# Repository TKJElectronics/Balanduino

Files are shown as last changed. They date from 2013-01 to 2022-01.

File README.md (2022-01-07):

# Balanduino
#### Developed by TKJ Electronics 2013-2022

The code is released under the GNU General Public License.
_________

This is the code for the Balanduino, the Open Source Balancing robot.

# Arduino compatible

To use the Balanduino as a normal Arduino board you need to add the hardware add-on to the Arduino IDE.

See the [Getting Started page](http://balanduino.tkjelectronics.dk/get-started) for more information.

# Hardware

The Balanduino hardware consist of an ATmega1284P running at 10MHz.

A MPU-6050 3-axis accelerometer and gyroscope.
The accelerometer and gyroscope readings are combined using a Kalman filter library. See my blog post: <http://blog.tkjelectronics.dk/2012/09/a-practical-approach-to-kalman-filter-and-how-to-implement-it/> and source <https://github.com/TKJElectronics/KalmanFilter> for more information.

USB Host support is implemented using the MAX3421E and the USB Host library: <https://github.com/felis/USB_Host_Shield_2.0>.

Two VNH5180 motor controller ICs is used to drive the two motors.

More information can be found at the Wiki article: <http://balanduino.tkjelectronics.dk/wiki/Overview>.

# Remote control

## Game controllers

To control the robot you can use the following game controllers:

* Normal PS3 Dualshock controller
* PS3 Navigation controller
* PS3 Move controller
* PS4 controller
* Xbox 360 wireless controller
* Wiimote including support for the Motion Plus and Nunchuck extension
* Wii U Pro controller

### Pairing

To pair with any of the PS3 controller please see the following section of the USB Host library readme: <https://github.com/felis/USB_Host_Shield_2.0#ps3-library>.

To pair with the PS4 controller send: ```CPP;``` via the serial monitor. Then hold down the Share button and then hold down the PS button without releasing the Share button. The PS4 controller will then start to blink rapidly indicating that it is in paring mode.

To use a Xbox 360 wireless controller you need a special receiver. More information can be seen at the following link: <https://github.com/felis/USB_Host_Shield_2.0#xbox-360-library>.

To pair with the Wiimote send: ```CPW;``` via the serial monitor and then press 1 and 2 at the same time on the Wiimote. On the Wii U Pro controller you should press on the sync button instead.

## Android App

It it also possible to control the robot and adjust the PID values and others variables using the following Android application:



Source: <https://github.com/TKJElectronics/BalanduinoAndroidApp>

## Computer applications

You can also use your Windows, Mac or Linux based computer by using the following Processing application: <https://github.com/TKJElectronics/BalanduinoProcessingApp>.

A dedicated Windows application is also available: <https://github.com/TKJElectronics/BalanduinoWindowsApp>.

## RC Transmitter

You can also use a RC transmitter. For now only Spektrum satellite receivers are supported.

You will need the following receiver and cable:

* <http://hobbyking.com/hobbyking/store/__46339__OrangeRx_R100_Spektrum_JR_DSM2_Compatible_Satellite_Receiver.html>
* <http://hobbyking.com/hobbyking/store/__24524__ZYX_S_DSM2_DSMJ_Satellite_Receiver_Cable.html>

After that simply connect the red wire to 5V, black to GND and the yellow one to RX0.

To bind with the satellite receiver send ```BS;``` via the serial monitor and then follow the instructions.

Note that you might need to disconnect the satellite receiver from RX0 if it is already sending data, as it will corrupt your command.

The video below shows a video demonstration of it being used together with some FPV equipment:

<a href="http://www.youtube.com/watch?v=tcFdWlAbc3s" target="_blank">Balanduino FPV demonstration</a>

# Video presentation

A video for the Kickstarter presentation can be seen below:

<a href="http://www.youtube.com/watch?v=_kQniPbg9zc" target="_blank">Kickstarter video presentation</a>

A video filmed with a GoPro mounted on the robot can be seen below:

<a href="http://www.youtube.com/watch?v=CvFcnb_9anM" target="_blank">GoPro demonstration</a>

# Calibration of the accelerometer

If the robot tilts to one of the sides when you receive the kit, you might need to calibrate the accelerometer.

This is done by simply sending ```AC;``` via the serial monitor. After that simply just follow the instructions.

# Download

To download the entire repository including all submodules run the following command in a terminal:

```bash
curl https://raw.githubusercontent.com/TKJElectronics/Balanduino/master/download.sh | sh
```

Or simply download the latest release: <https://github.com/TKJElectronics/Balanduino/releases/download/1.2.0/Balanduino-1.2.0.zip>.

If you want to clone the project then use the recursive command to clone all the submodules as well:

```bash
git clone --recursive https://github.com/TKJElectronics/Balanduino.git
```

</br>

For more information visit the official website: <http://balanduino.tkjelectronics.dk/>, the forum: <http://balanduino.tkjelectronics.dk/forum> or feel free to contact us at <support@tkjelectronics.dk>.

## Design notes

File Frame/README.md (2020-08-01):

# Balanduino Frame
#### Developed by Kristian Lauszus and Thomas Jespersen, TKJ Electronics 2013-2015

The frame is released under the [Attribution-NonCommercial-ShareAlike 3.0 Unported](http://creativecommons.org/licenses/by-nc-sa/3.0/).
_________

This is the drawings for the three laser cut layers used for the Balanduino.

To open the files you will need to download and install [SolidWorks](http://www.solidworks.com/) or you can also import the .DXF file into any preferred CAD program.

For more information visit the official website: <http://balanduino.net/>, the forum: <http://forum.balanduino.net/> or feel free to contact us at <support@tkjelectronics.dk>.

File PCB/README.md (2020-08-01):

# Balanduino PCB
#### Developed by Kristian Lauszus and Thomas Jespersen, TKJ Electronics 2013-2015

The PCB is released under the [Attribution-NonCommercial-ShareAlike 3.0 Unported](http://creativecommons.org/licenses/by-nc-sa/3.0/).
_________

This is the PCB for the Balanduino.

To open the files you will need to download and install [EAGLE](http://www.cadsoftusa.com/download-eagle/).

For more information visit the official website: <http://balanduino.net/>, the forum: <http://forum.balanduino.net/> or feel free to contact us at <support@tkjelectronics.dk>.

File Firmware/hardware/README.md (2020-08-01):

# Balanduino hardware add-on
#### Developed by Kristian Lauszus, TKJ Electronics 2013-2020

The code is released under the GNU General Public License.
_________

This is the Balanduino hardware add-on for the Arduino IDE.

See the [Getting Started page](http://balanduino.tkjelectronics.dk/get-started) for more information.

For more information see the following sites: <http://www.arduino.cc/en/Guide/Environment#thirdpartyhardware>, <http://code.google.com/p/arduino/wiki/Platforms1>, and <https://github.com/arduino/Arduino/wiki/Arduino-IDE-1.5---3rd-party-Hardware-specification> or send us an email at <support@tkjelectronics.dk>.

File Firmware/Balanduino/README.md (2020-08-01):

# Balanduino Arduino code
#### Developed by Kristian Lauszus, TKJ Electronics 2013-2020

The code is released under the GNU General Public License.
_________

This is the Arduino code for the Balanduino balancing robot.

To compile the sketch you will need the newest version of the [Arduino IDE](http://arduino.cc/en/Main/Software).

Then open the sketch by clicking on [Balanduino.ino](Balanduino.ino).

See the [Getting Started page](http://balanduino.tkjelectronics.dk/get-started) for more information.

Advanced users can also use the included [Makefile](Makefile) if they prefer.

[Balanduino_rev12.hex](Balanduino_rev12.hex) and [Balanduino_rev13.hex](Balanduino_rev13.hex) contains the latest compiled code for revision 1.2 and older and revision 1.3 respectively.

For more information visit the official website: <http://balanduino.tkjelectronics.dk>, the forum: <http://balanduino.tkjelectronics.dk/forum> or feel free to contact us at <support@tkjelectronics.dk>.

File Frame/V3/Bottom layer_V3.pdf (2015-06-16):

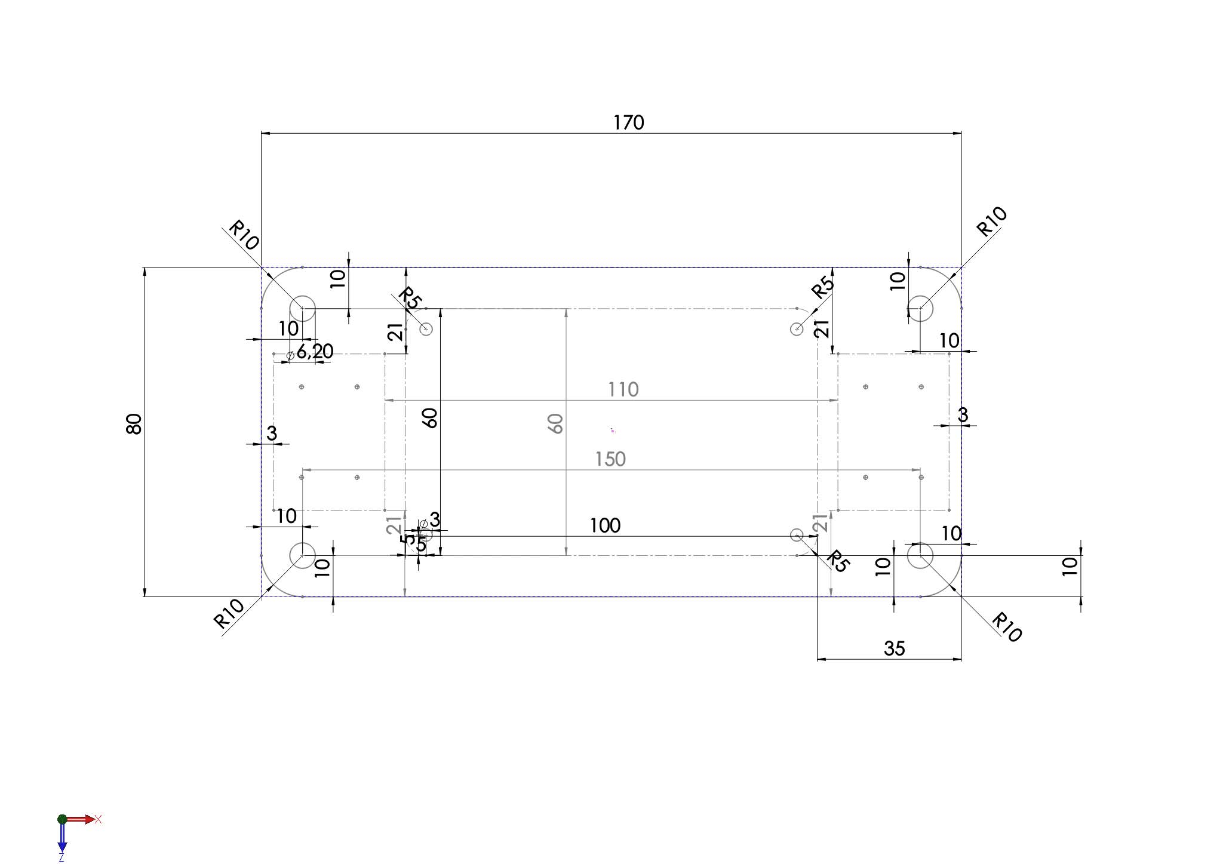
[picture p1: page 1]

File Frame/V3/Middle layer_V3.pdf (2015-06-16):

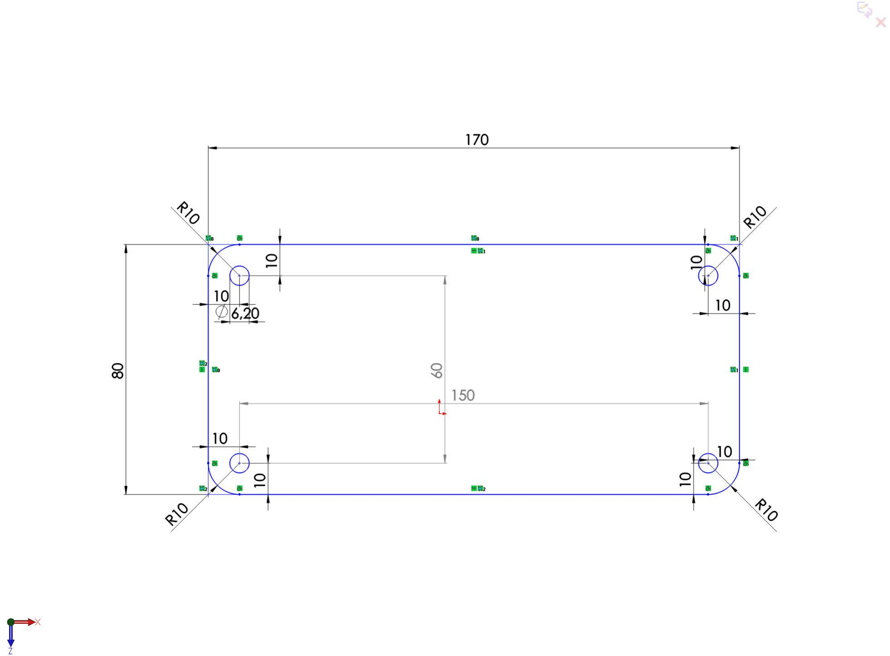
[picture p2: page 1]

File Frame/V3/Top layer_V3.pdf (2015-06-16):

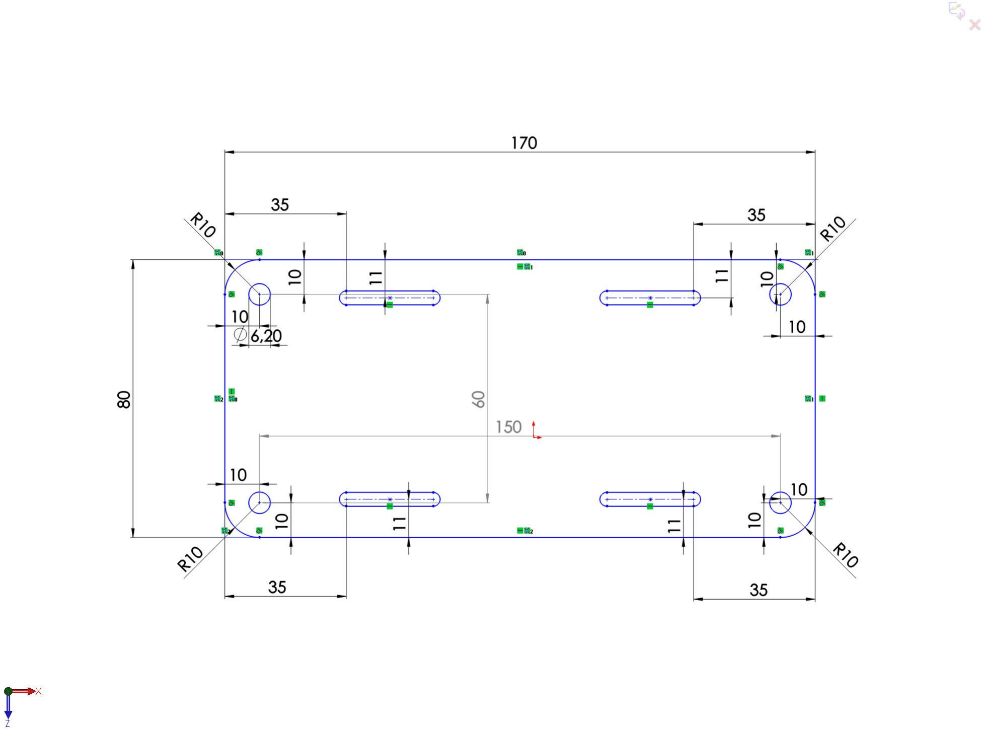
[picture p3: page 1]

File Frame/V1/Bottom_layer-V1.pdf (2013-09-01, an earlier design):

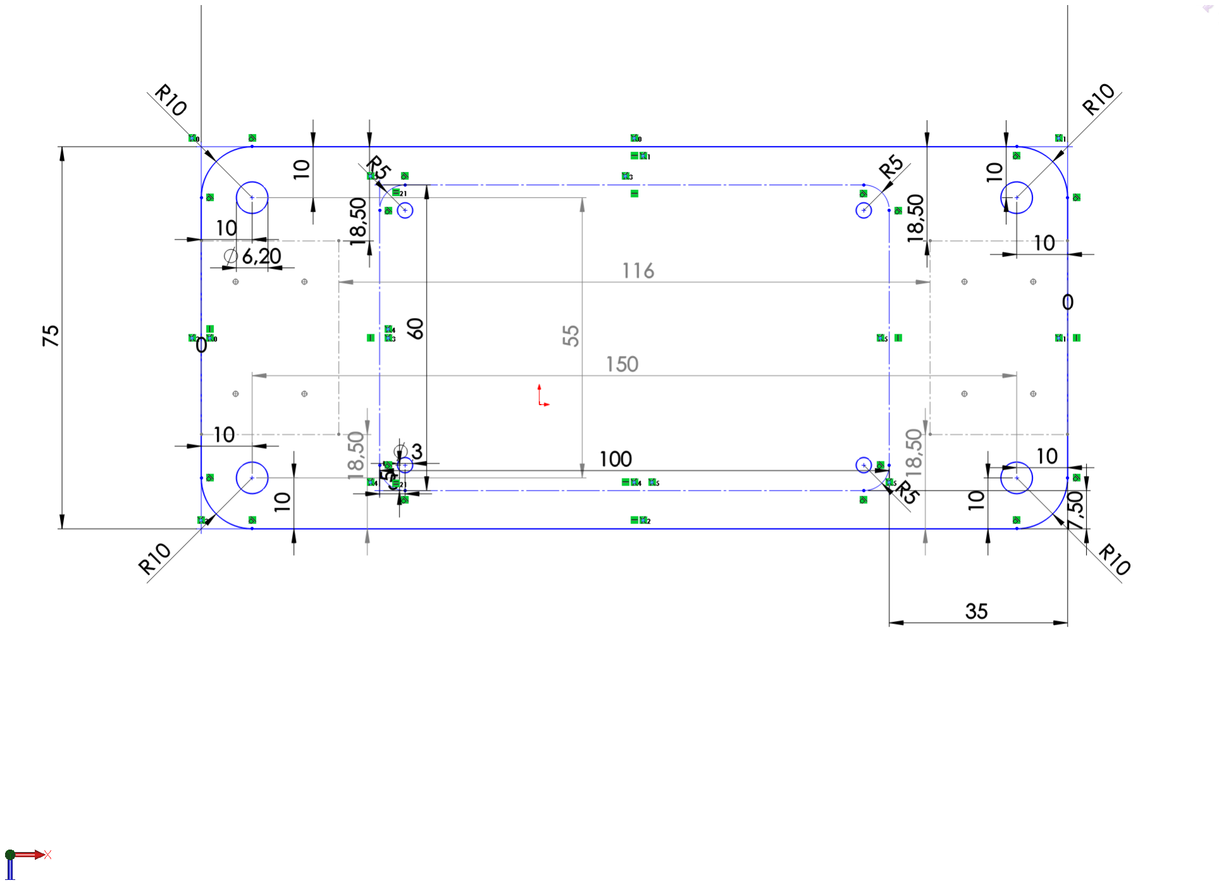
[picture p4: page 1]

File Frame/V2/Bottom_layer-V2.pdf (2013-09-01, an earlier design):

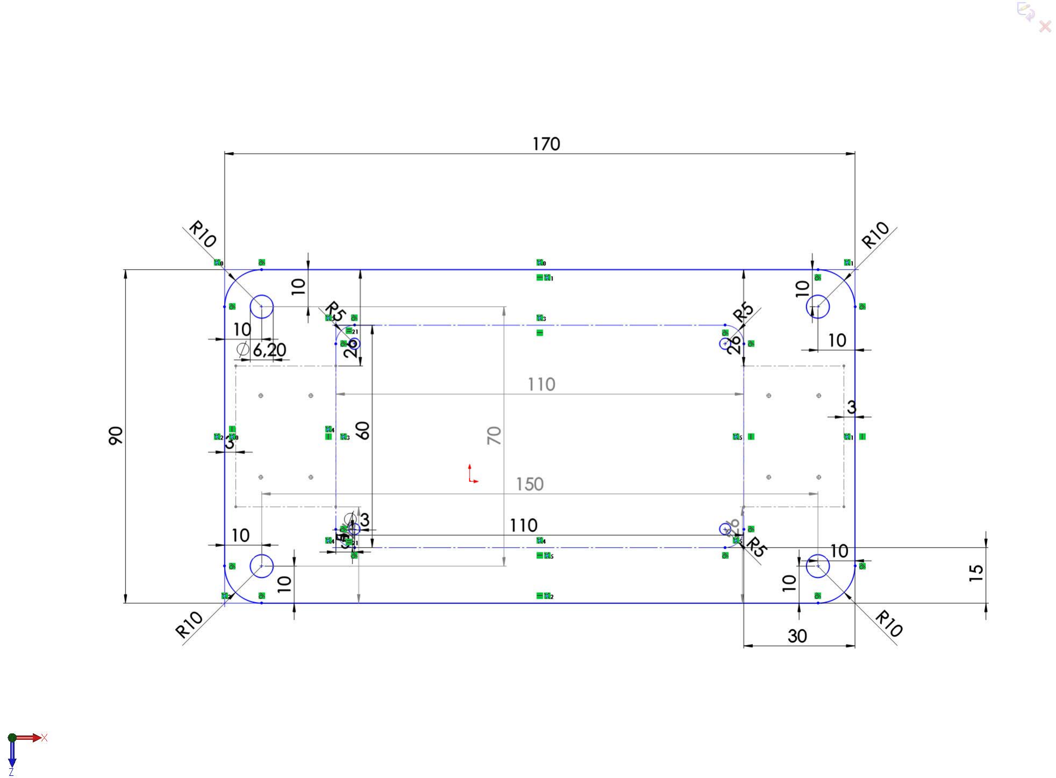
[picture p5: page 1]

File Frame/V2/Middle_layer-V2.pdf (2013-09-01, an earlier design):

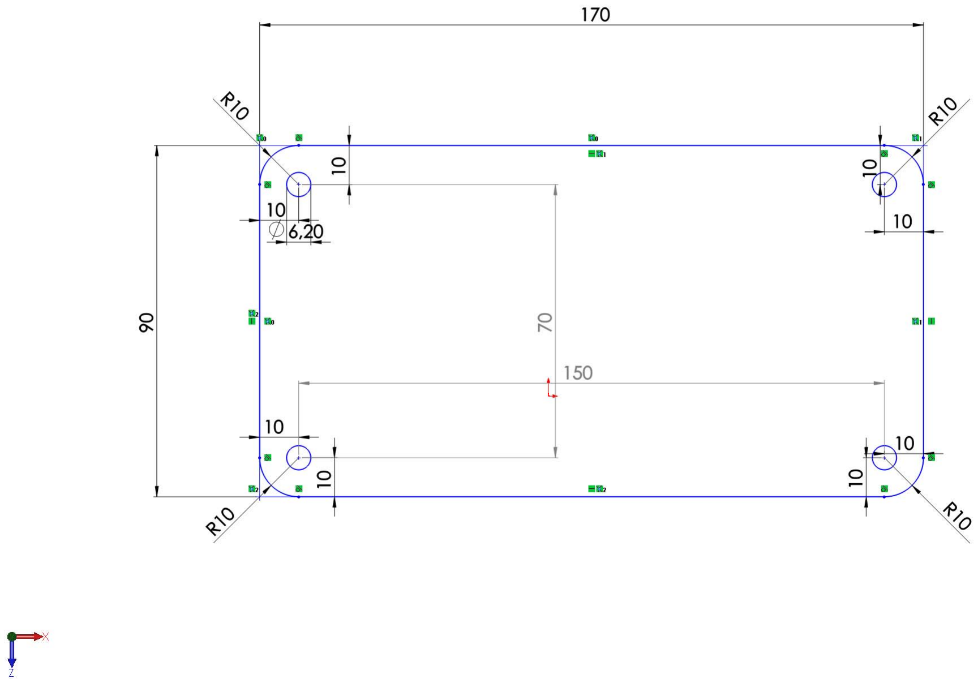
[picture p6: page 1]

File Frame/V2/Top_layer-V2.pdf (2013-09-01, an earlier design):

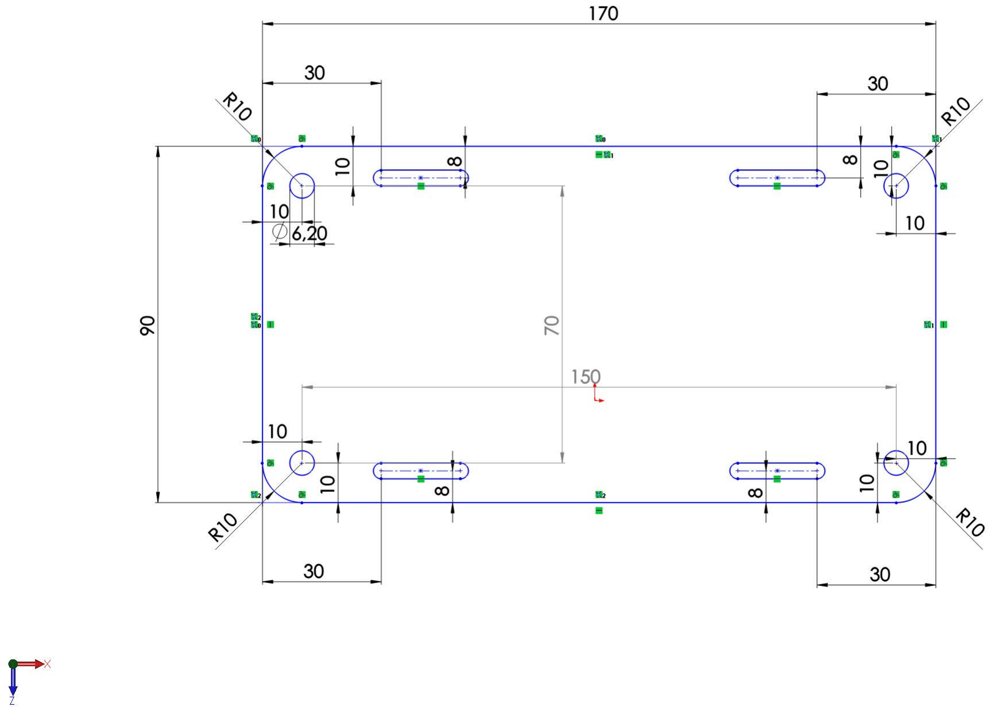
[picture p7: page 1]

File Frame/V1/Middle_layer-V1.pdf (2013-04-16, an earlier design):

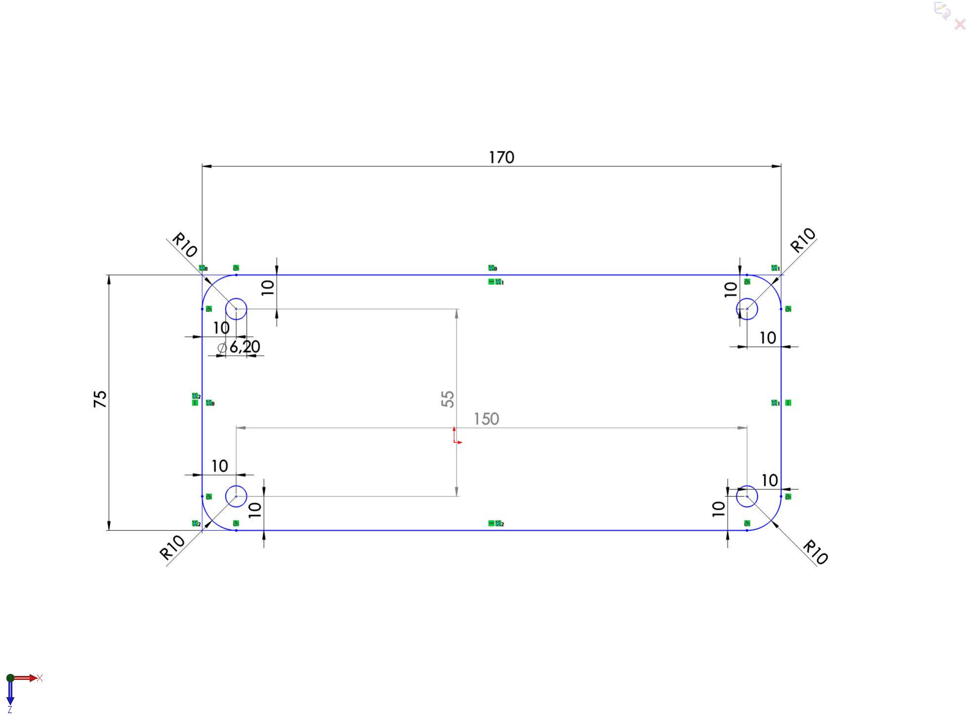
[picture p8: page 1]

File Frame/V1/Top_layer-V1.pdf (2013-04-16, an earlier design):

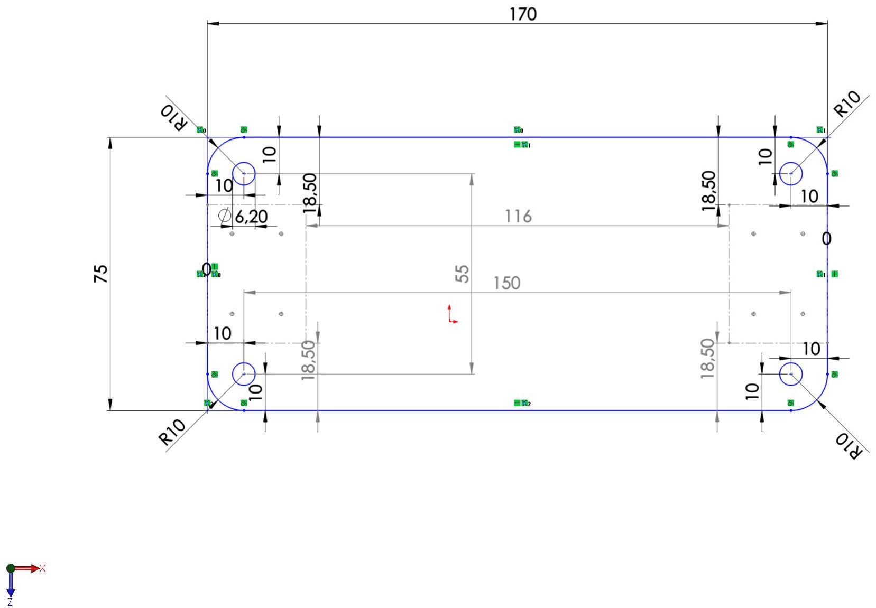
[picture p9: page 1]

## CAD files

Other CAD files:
Frame/V3/Top layer_V3.SLDPRT
Frame/V3/Bottom layer_V3.SLDPRT
Frame/V3/Middle layer_V3.SLDPRT
Frame/V1/Top_layer-V1.SLDPRT
Frame/V2/Top_layer-V2.SLDPRT
Frame/V1/Bottom_layer-V1.SLDPRT
Frame/V2/Middle_layer-V2.SLDPRT
Frame/V1/Middle_layer-V1.SLDPRT
Frame/V2/Bottom_layer-V2.SLDPRT
Frame/V1/Bottom_layer-V1.DXF
Frame/V1/Middle_layer-V1.DXF
Frame/V1/Top_layer-V1.DXF
Frame/V2/Bottom_layer-V2.DXF
Frame/V2/Middle_layer-V2.DXF
Frame/V2/Top_layer-V2.DXF
Frame/V3/Bottom layer_V3.DXF
Frame/V3/Middle layer_V3.DXF
Frame/V3/Top layer_V3.DXF

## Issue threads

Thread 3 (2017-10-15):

No waiting needed after Wire.requestFrom().

Koepel, 2017-10-15:
See: https://github.com/TKJElectronics/KalmanFilter/issues/9

Lauszus, 2018-06-23:
Since this does not have real benefits and the code in the library have been proven to work with multiple different kind of microcontrollers, then I see no real benefit by changing it. If you really want to change it, then you can submit a PR and do some testing.

Closed 2018-06-23.

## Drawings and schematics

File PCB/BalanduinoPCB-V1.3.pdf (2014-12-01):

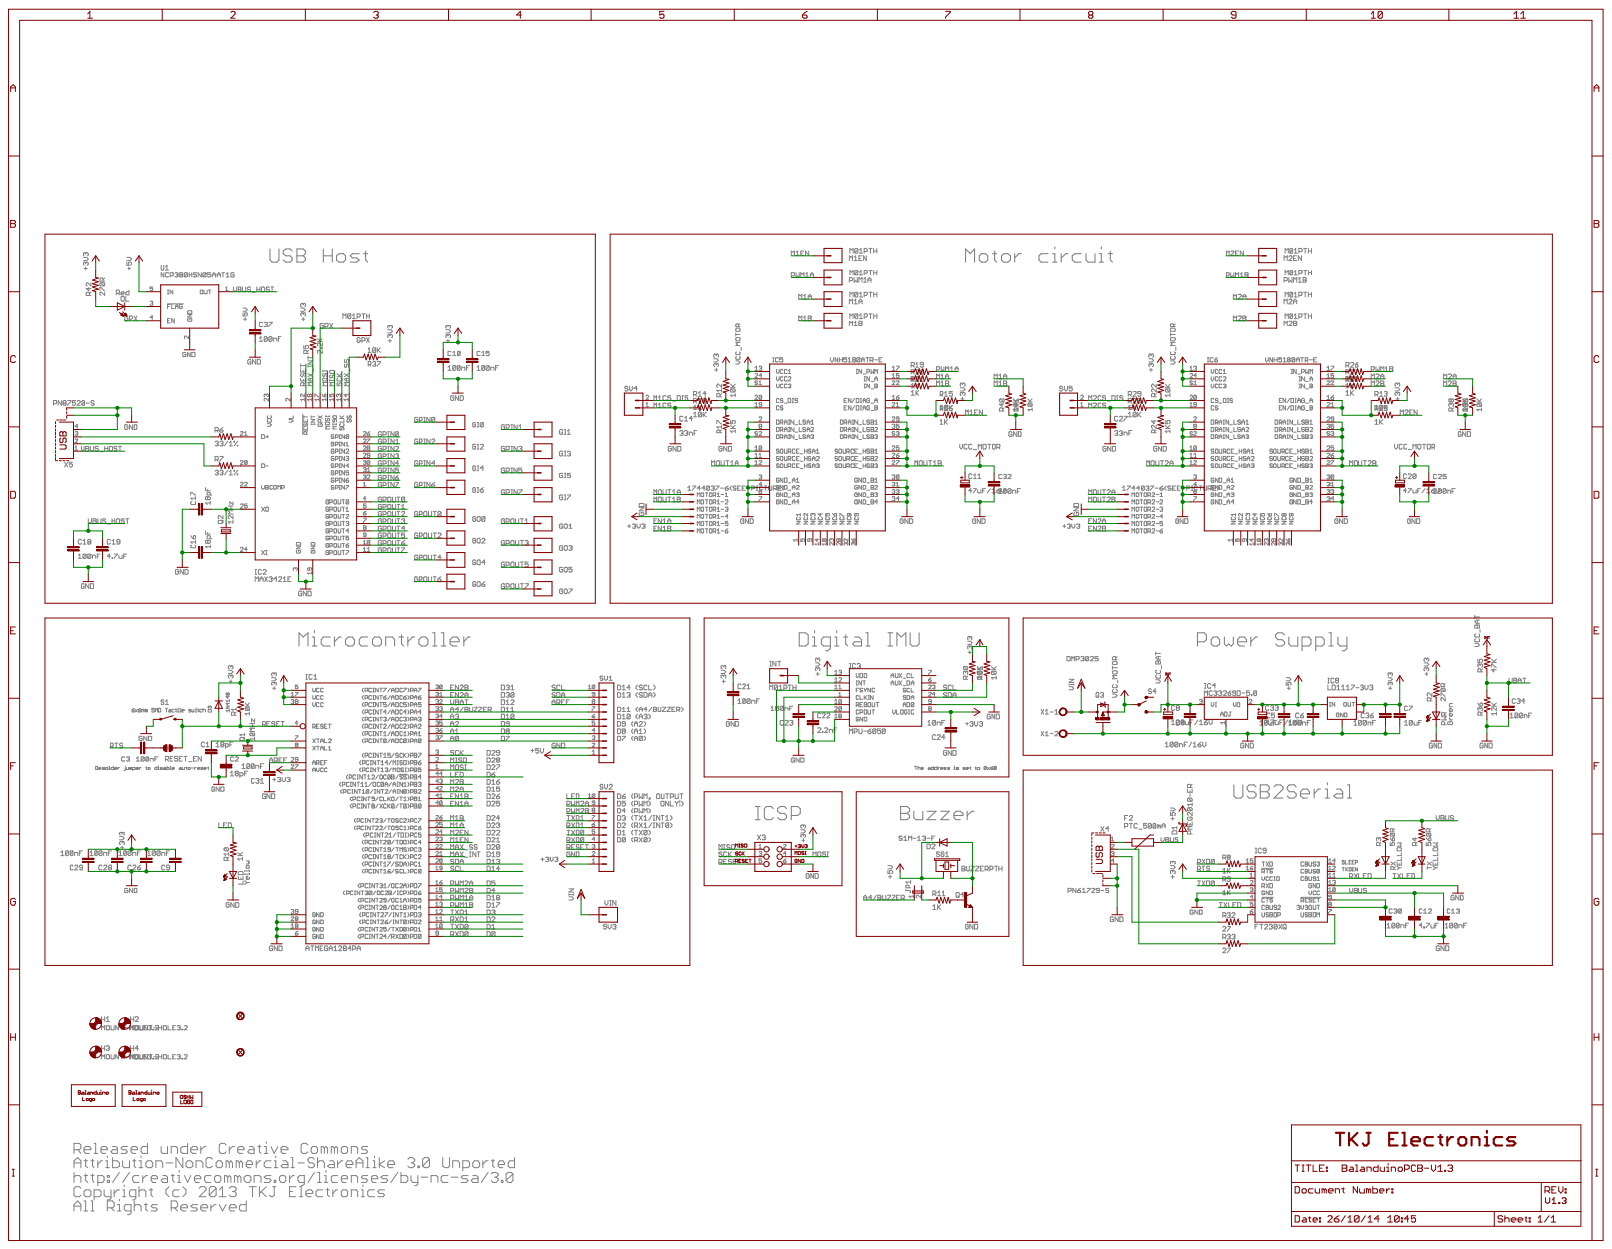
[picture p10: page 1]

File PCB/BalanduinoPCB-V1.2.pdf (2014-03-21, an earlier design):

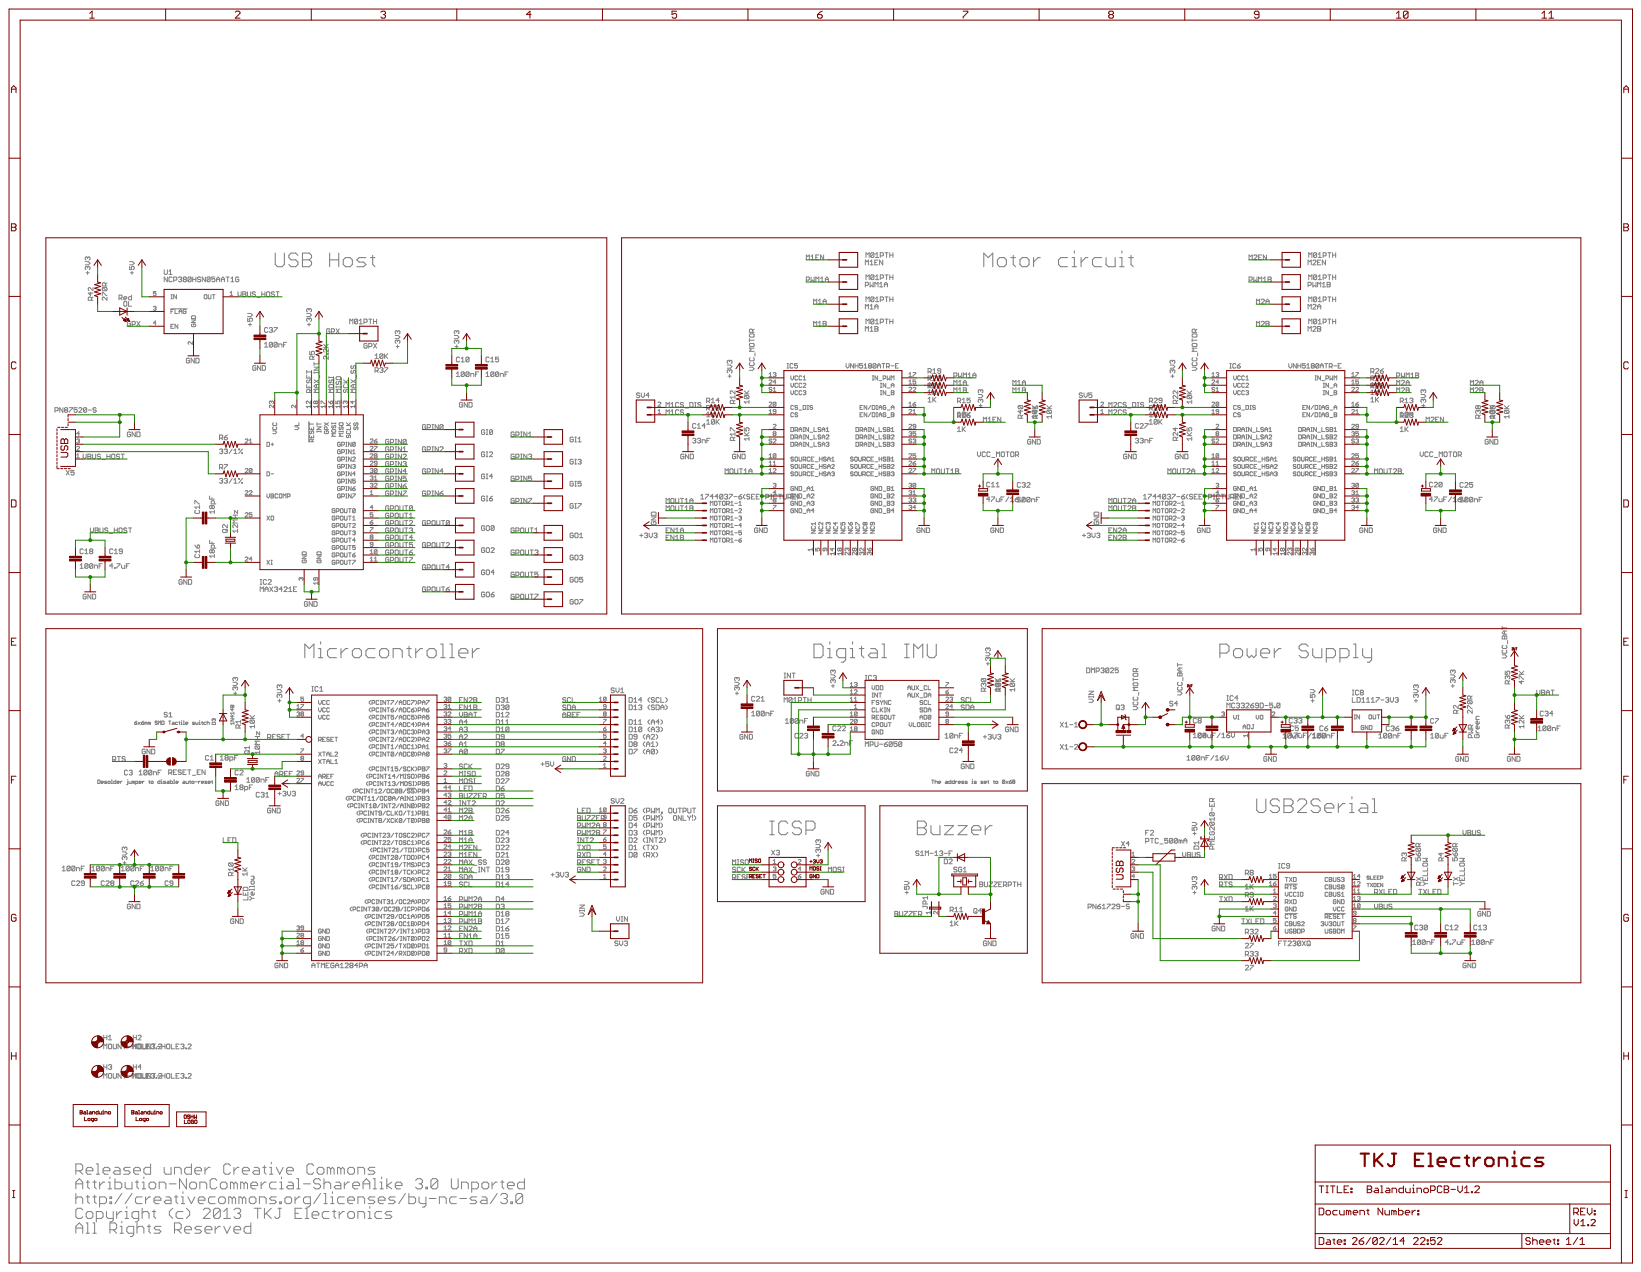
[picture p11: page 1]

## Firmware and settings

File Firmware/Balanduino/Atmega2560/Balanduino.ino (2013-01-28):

/*
 * The code is released under the GNU General Public License.
 * Developed by Kristian Lauszus
 * This is the algorithm for the Balanduino balancing robot.
 * It can be controlled by either an Android app or a Processing application via bluetooth.
 * The Android app can be found at the following link: https://github.com/TKJElectronics/BalanduinoAndroidApp
 * The Processing application can be found here: https://github.com/TKJElectronics/BalanduinoProcessingApp
 * It can also be controlled by a PS3, Wii or a Xbox controller
 * For details, see http://blog.tkjelectronics.dk/2012/02/the-balancing-robot/
 */

#include "Balanduino.h"

/* 
 * These are all open source libraries written by Kristian Lauszus, TKJ Electronics
 * The USB libraries are located at the following link: https://github.com/felis/USB_Host_Shield_2.0
 */
#include <Kalman.h> // Kalman filter library see: http://blog.tkjelectronics.dk/2012/09/a-practical-approach-to-kalman-filter-and-how-to-implement-it/
#include <XBOXRECV.h>
#include <SPP.h>
#include <PS3BT.h>
#include <Wii.h>

// Create the Kalman library instance
Kalman kalman; // See https://github.com/TKJElectronics/KalmanFilter for source code

// This will take care of all USB communication
USB Usb;

// You have to connect a Xbox wireless receiver to the Arduino to control it with a wirelessly Xbox controller
XBOXRECV Xbox(&Usb); // Uncomment DEBUG in "XBOXRECV.cpp" to save space
BTD Btd(&Usb); // This is the main Bluetooth library, it will take care of all the Bluetooth communication - Uncomment DEBUG in "BTD.cpp" to save space
SPP SerialBT(&Btd,"Balanduino","0000"); // Also uncomment DEBUG in "SPP.cpp"
PS3BT PS3(&Btd,0x00,0x15,0x83,0x3D,0x0A,0x57); // Also remember to uncomment DEBUG in "PS3BT.cpp" to save space
WII Wii(&Btd); // Also uncomment DEBUG in "Wii.cpp"

// You have to pair with your Wiimote first by creating the instance like this and the press 1+2 on the Wiimote - you only have to do this once
//WII Wii(&Btd,PAIR);

void setup() {
  /* Setup encoders */
  pinMode(leftEncoder1,INPUT);
  pinMode(leftEncoder2,INPUT);
  pinMode(rightEncoder1,INPUT);
  pinMode(rightEncoder2,INPUT); 
  attachInterrupt(0,leftEncoder,RISING); // pin 2
  attachInterrupt(1,rightEncoder,RISING); // pin 3

  /* Setup motor pins to output */
  sbi(leftPwmPortDirection,leftPWM);
  sbi(leftPortDirection,leftA);
  sbi(leftPortDirection,leftB);
  sbi(rightPwmPortDirection,rightPWM);
  sbi(rightPortDirection,rightA);
  sbi(rightPortDirection,rightB);  

  /* Set PWM frequency to 20kHz - see the datasheet http://www.atmel.com/Images/doc8025.pdf page 128-135 */
  // Set up PWM, Phase and Frequency Correct on pin 9 (OC1A) & pin 10 (OC1B) with ICR1 as TOP using Timer1
  TCCR1B = _BV(WGM13) | _BV(CS10); // Set PWM Phase and Frequency Correct with ICR1 as TOP and no prescaling
  ICR1H = (PWMVALUE >> 8); // ICR1 is the TOP value - this is set so the frequency is equal to 20kHz
  ICR1L = (PWMVALUE & 0xFF);

  /* Enable PWM on pin 9 (OC1A) & pin 10 (OC1B) */
  // Clear OC1A/OC1B on compare match when up-counting
  // Set OC1A/OC1B on compare match when downcountin
  TCCR1A = _BV(COM1A1) | _BV(COM1B1);
  setPWM(leftPWM,0); // Turn off pwm on both pins
  setPWM(rightPWM,0);

  /* Setup pin for buzzer to beep when finished calibrating */
  pinMode(buzzer,OUTPUT);  

  /* Setup IMU Inputs */
  analogReference(EXTERNAL); // Set voltage reference to 3.3V by connecting AREF to 3.3V
  pinMode(gyroY,INPUT);
  pinMode(accY,INPUT);
  pinMode(accZ,INPUT);      

  if (Usb.Init() == -1) // Check if USB Host Shield is working
    while(1); // Halt

  /* Calibrate the gyro and accelerometer relative to ground */
  calibrateSensors();
  
  /* Beep to indicate that it is now ready */
  digitalWrite(buzzer,HIGH);
  delay(100);  
  digitalWrite(buzzer,LOW);

  /* Setup timing */
  loopStartTime = micros();
  timer = loopStartTime;
}

void loop() {
  /* Calculate pitch */
  accYangle = getAccY();
  gyroYrate = getGyroYrate();
  gyroAngle += gyroYrate*((double)(micros()-timer)/1000000);
  // See my guide for more info about calculation the angles and the Kalman filter: http://arduino.cc/forum/index.php/topic,58048.0.htm
  pitch = kalman.getAngle(accYangle, gyroYrate, (double)(micros() - timer)/1000000); // Calculate the angle using a Kalman filter
  timer = micros();
  //Serial.print(accYangle);Serial.print('\t');Serial.print(gyroAngle);Serial.print('\t');Serial.println(pitch);

  /* Drive motors */
  // If the robot is laying down, it has to be put in a vertical position before it starts balancing
  // If it's already balancing it has to be ±45 degrees before it stops trying to balance
  if((layingDown && (pitch < 170 || pitch > 190)) || (!layingDown && (pitch < 135 || pitch > 225))) {
    layingDown = true; // The robot is in a unsolvable position, so turn off both motors and wait until it's vertical again
    stopAndReset();
  } 
  else {
    layingDown = false; // It's no longer laying down
    PID(targetAngle,targetOffset,turningOffset);        
  }

  /* Update wheel velocity every 100ms */
  loopCounter++;
  if (loopCounter == 10) {
    loopCounter = 0; // Reset loop counter
    wheelPosition = readLeftEncoder() + readRightEncoder();
    wheelVelocity = wheelPosition - lastWheelPosition;
    lastWheelPosition = wheelPosition;
    if (abs(wheelVelocity) <= 20 && !stopped) { // Set new targetPosition if braking
      targetPosition = wheelPosition;
      stopped = true;
    }
  }

  /* Read the Bluetooth dongle */
  readBTD();    
  
  if(SerialBT.connected) {
    Usb.Task();
    if(sendPIDValues) {
      sendPIDValues = false;
      strcpy(stringBuf,"P,");
      strcat(stringBuf,SerialBT.doubleToString(Kp,2));
      strcat(stringBuf,",");
      strcat(stringBuf,SerialBT.doubleToString(Ki,2));
      strcat(stringBuf,",");
      strcat(stringBuf,SerialBT.doubleToString(Kd,2));
      strcat(stringBuf,",");
      strcat(stringBuf,SerialBT.doubleToString(targetAngle,2));
      SerialBT.println(stringBuf);
      dataCounter = 0; // Set the counter to 0, to prevent it from sending data in the next loop
    } else if(sendData) {
      switch(dataCounter) {
        case 0:      
          strcpy(stringBuf,"V,");
          strcat(stringBuf,SerialBT.doubleToString(accYangle,2));
          strcat(stringBuf,",");
          strcat(stringBuf,SerialBT.doubleToString(gyroAngle,2));
          strcat(stringBuf,",");
          strcat(stringBuf,SerialBT.doubleToString(pitch,2));
          SerialBT.println(stringBuf);
          break;
      }    
      dataCounter++;
      if(dataCounter > 4)
        dataCounter = 0;    
    }
  }

  /* Use a time fixed loop */
  lastLoopUsefulTime = micros() - loopStartTime;
  if (lastLoopUsefulTime < STD_LOOP_TIME) {
    while((micros() - loopStartTime) < STD_LOOP_TIME)
        Usb.Task();
  }
  //Serial.print(lastLoopUsefulTime);Serial.print(',');Serial.println(micros() - loopStartTime);
  loopStartTime = micros();    
}
void PID(double restAngle, double offset, double turning) {
  /* Steer robot */
  if (steerForward) {
    offset += (double)wheelVelocity/velocityScaleMove; // Scale down offset at high speed and scale up when reversing
    restAngle -= offset;
  } 
  else if (steerBackward) {
    offset -= (double)wheelVelocity/velocityScaleMove; // Scale down offset at high speed and scale up when reversing
    restAngle += offset;
  }
  /* Brake */
  else if (steerStop) {
    long positionError = wheelPosition - targetPosition;
    if (abs(positionError) > zoneA) // Inside zone A
      restAngle -= (double)positionError/positionScaleA;
    else if (abs(positionError) > zoneB) // Inside zone B
      restAngle -= (double)positionError/positionScaleB;
    else // Inside zone C
      restAngle -= (double)positionError/positionScaleC;   
    restAngle -= (double)wheelVelocity/velocityScaleStop;
    if (restAngle < 160) // Limit rest Angle
      restAngle = 160;
    else if (restAngle > 200)
      restAngle = 200;
  }
  /* Update PID values */
  double error = (restAngle - pitch);
  double pTerm = Kp * error;
  iTerm += Ki * error;
  double dTerm = Kd * (error - lastError);
  lastError = error;
  double PIDValue = pTerm + iTerm + dTerm;

  /* Steer robot sideways */
  double PIDLeft;
  double PIDRight;
  if (steerLeft) {
    turning -= abs((double)wheelVelocity/velocityScaleTurning); // Scale down at high speed
    if(turning < 0)
      turning = 0;
    PIDLeft = PIDValue-turning;
    PIDRight = PIDValue+turning;
  }
  else if (steerRight) {
    turning -= abs((double)wheelVelocity/velocityScaleTurning); // Scale down at high speed
    if(turning < 0)
      turning = 0;
    PIDLeft = PIDValue+turning;
    PIDRight = PIDValue-turning;
  }
  else {
    PIDLeft = PIDValue;
    PIDRight = PIDValue;
  }

  PIDLeft *= 0.95; // compensate for difference in the motors

  /* Set PWM Values */
  if (PIDLeft >= 0)
    moveMotor(left, forward, PIDLeft);
  else
    moveMotor(left, backward, PIDLeft * -1);
  if (PIDRight >= 0)
    moveMotor(right, forward, PIDRight);
  else
    moveMotor(right, backward, PIDRight * -1);
}
void readBTD() {
  Usb.Task();
  if(SerialBT.connected) { // The SPP connection won't return data as fast as the controllers, so we will handle it separately
    if(SerialBT.available()) {
      char input[30];
      uint8_t i = 0;
      while (1) {
        input[i] = SerialBT.read();
        if(input[i] == 0) // Error while reading the string
          return;
        if (input[i] == ';') // Keep reading until it reads a semicolon
          break;
        i++;
      }      
      /*Serial.print("Data: ");
      Serial.write((uint8_t*)input,i);
      Serial.println();*/
      if(input[0] == 'A') { // Abort
        stopAndReset();
        while(SerialBT.read() != 'C') // Wait until continue is send
          Usb.Task();
      } 
      
      /* Set PID and target angle */
      else if(input[0] == 'P') {
        strtok(input, ","); // Ignore 'P'
        Kp = atof(strtok(NULL, ";"));
      } else if(input[0] == 'I') {
        strtok(input, ","); // Ignore 'I'
        Ki = atof(strtok(NULL, ";"));
      } else if(input[0] == 'D') {
        strtok(input, ","); // Ignore 'D'
        Kd = atof(strtok(NULL, ";"));  
      } else if(input[0] == 'T') { // Target Angle
        strtok(input, ","); // Ignore 'T'
        targetAngle = atof(strtok(NULL, ";"));  
      } else if(input[0] == 'G') { // The processing/Android application sends when it need the current values
        if(input[1] == 'P') // PID Values
          sendPIDValues = true;
        else if(input[1] == 'B') // Begin
          sendData = true; // Send output to processing/Android application
        else if(input[1] == 'S') // Stop
          sendData = false; // Stop sending output to processing/Android application
      }
      /* Remote control */
      else if(input[0] == 'S') // Stop
        steer(stop);
      else if(input[0] == 'J') { // Joystick
        strtok(input, ","); // Ignore 'J'
        sppData1 = atof(strtok(NULL, ",")); // x-axis
        sppData2 = atof(strtok(NULL, ";")); // y-axis
        steer(joystick);
      }
      else if(input[0] == 'M') { // IMU
        strtok(input, ","); // Ignore 'M'
        sppData1 = atof(strtok(NULL, ",")); // Pitch
        sppData2 = atof(strtok(NULL, ";")); // Roll
        steer(imu);
        //SerialBT.printNumberln(sppData1);
        //SerialBT.printNumberln(sppData2);
      }
    }
  } else {
    commandSent = false; // We use this to detect when there has already been sent a command by one of the controllers
    if(PS3.PS3Connected) {
      if(PS3.getButtonClick(PS))
        PS3.disconnect();
      else if(PS3.getButtonPress(SELECT)) {
        stopAndReset();
        while(!PS3.getButtonPress(START))
          Usb.Task();        
      }
      else if((PS3.getAnalogHat(LeftHatY) < 117) || (PS3.getAnalogHat(RightHatY) < 117) || (PS3.getAnalogHat(LeftHatY) > 137) || (PS3.getAnalogHat(RightHatY) > 137))
        steer(updatePS3);
    } 
    else if(PS3.PS3NavigationConnected) {
      if(PS3.getButtonClick(PS))
        PS3.disconnect();
      else if(PS3.getAnalogHat(LeftHatX) > 200 || PS3.getAnalogHat(LeftHatX) < 55 || PS3.getAnalogHat(LeftHatY) > 137 || PS3.getAnalogHat(LeftHatY) < 117)
        steer(updatePS3);
    } 
    if(Wii.wiimoteConnected && !commandSent) {
      if(Wii.getButtonClick(HOME)) // You can use getButtonPress to see if the button is held down
        Wii.disconnect();
      else if(Wii.getButtonPress(B))
        steer(updateWii);
      else if(Wii.nunchuckConnected && (Wii.getAnalogHat(HatX) > 137 || Wii.getAnalogHat(HatX) < 117 || Wii.getAnalogHat(HatY) > 137 || Wii.getAnalogHat(HatY) < 117))
        steer(updateWii);
    } 
    if(Xbox.XboxReceiverConnected && Xbox.Xbox360Connected[0] && !commandSent) { // We will only read from the first controller
      if(Xbox.getButtonPress(0,BACK)) {
        stopAndReset();
        while(!Xbox.getButtonPress(0,START))
          Usb.Task();
      }
      else if((Xbox.getAnalogHat(0,LeftHatY) < -7500) || (Xbox.getAnalogHat(0,RightHatY) < -7500) || (Xbox.getAnalogHat(0,LeftHatY) > 7500) || (Xbox.getAnalogHat(0,RightHatY) > 7500))
        steer(updateXbox);
    }
    if(!commandSent) // If there hasn't been send a command by now, then send stop
      steer(stop);
  }
}
void steer(Command command) {
  commandSent = true; // Used to see if there has already been send a command or not
    
  // Set all false
  steerForward = false;
  steerBackward = false;
  steerStop = false;
  steerLeft = false;
  steerRight = false;
  if(command == joystick) {    
    if(sppData2 > 0) {
      targetOffset = scale(sppData2,0,1,0,7);        
      steerForward = true;
    } else if(sppData2 < 0) {
      targetOffset = scale(sppData2,0,-1,0,7);
      steerBackward = true;
    } 
    if(sppData1 > 0) {
      turningOffset = scale(sppData1,0,1,0,20);        
      steerRight = true;
    } else if(sppData1 < 0) {
      turningOffset = scale(sppData1,0,-1,0,20);
      steerLeft = true;     
    }
  } else if(command == imu) {
      if(sppData2 > 0) {
        targetOffset = scale(sppData2,0,36,0,7);        
        steerForward = true;
      }     
      else if(sppData2 < 0) {
        targetOffset = scale(sppData2,0,-36,0,7);
        steerBackward = true;
      }
      if(sppData1 > 0) {
        turningOffset = scale(sppData1,0,45,0,20);        
        steerLeft = true;
      }
      else if(sppData1 < 0) {
        turningOffset = scale(sppData1,0,-45,0,20);
        steerRight = true;     
      }
  } else if(command == updatePS3) {
    if(PS3.PS3Connected) {
      if(PS3.getAnalogHat(LeftHatY) < 117 && PS3.getAnalogHat(RightHatY) < 117) {
        targetOffset = scale(PS3.getAnalogHat(LeftHatY)+PS3.getAnalogHat(RightHatY),232,0,0,7); // Scale from 232-0 to 0-7
        steerForward = true;
      } else if(PS3.getAnalogHat(LeftHatY) > 137 && PS3.getAnalogHat(RightHatY) > 137) {
        targetOffset = scale(PS3.getAnalogHat(LeftHatY)+PS3.getAnalogHat(RightHatY),276,510,0,7); // Scale from 276-510 to 0-7
        steerBackward = true;
      }
      if(((int)PS3.getAnalogHat(LeftHatY) - (int)PS3.getAnalogHat(RightHatY)) > 15) {
        turningOffset = scale(abs(PS3.getAnalogHat(LeftHatY) - PS3.getAnalogHat(RightHatY)),0,255,0,20); // Scale from 0-255 to 0-20
        steerLeft = true;      
      } else if (((int)PS3.getAnalogHat(RightHatY) - (int)PS3.getAnalogHat(LeftHatY)) > 15) {   
        turningOffset = scale(abs(PS3.getAnalogHat(LeftHatY) - PS3.getAnalogHat(RightHatY)),0,255,0,20); // Scale from 0-255 to 0-20  
        steerRight = true;  
      }  
    } else { // It must be a Navigation controller then
      if(PS3.getAnalogHat(LeftHatY) < 117) {
        targetOffset = scale(PS3.getAnalogHat(LeftHatY),116,0,0,7); // Scale from 116-0 to 0-7
        steerForward = true;
      } else if(PS3.getAnalogHat(LeftHatY) > 137) {
        targetOffset = scale(PS3.getAnalogHat(LeftHatY),138,255,0,7); // Scale from 138-255 to 0-7
        steerBackward = true;
      }
      if(PS3.getAnalogHat(LeftHatX) < 55) {
        turningOffset = scale(PS3.getAnalogHat(LeftHatX),54,0,0,20); // Scale from 54-0 to 0-20
        steerLeft = true;     
      } else if(PS3.getAnalogHat(LeftHatX) > 200) {
        turningOffset = scale(PS3.getAnalogHat(LeftHatX),201,255,0,20); // Scale from 201-255 to 0-20
        steerRight = true;
      }
    }
  } else if(command == updateWii) {
    if(Wii.getButtonPress(B)) {
      if(Wii.getPitch() > 180) {
        targetOffset = scale(Wii.getPitch(),180,216,0,7);        
        steerForward = true;
      }     
      else if(Wii.getPitch() < 180) {
        targetOffset = scale(Wii.getPitch(),180,144,0,7);
        steerBackward = true;
      }
      if(Wii.getRoll() > 180) {
        turningOffset = scale(Wii.getRoll(),180,225,0,20);        
        steerRight = true;
      }
      else if(Wii.getRoll() < 180) {
        turningOffset = scale(Wii.getRoll(),180,135,0,20);
        steerLeft = true;     
      }
    }
    else {
      if(Wii.getAnalogHat(HatY) > 137) {
        targetOffset = scale(Wii.getAnalogHat(HatY),138,230,0,7);
        steerForward = true;
      } 
      else if(Wii.getAnalogHat(HatY) < 117) {
        targetOffset = scale(Wii.getAnalogHat(HatY),116,25,0,7);
        steerBackward = true;
      }
      if(Wii.getAnalogHat(HatX) > 137) {
        turningOffset = scale(Wii.getAnalogHat(HatX),138,230,0,20);
        steerRight = true;     
      } 
      else if(Wii.getAnalogHat(HatX) < 117) {
        turningOffset = scale(Wii.getAnalogHat(HatX),116,25,0,20);
        steerLeft = true;
      }
    }
  } else if(command == updateXbox) {
    if(Xbox.getAnalogHat(0,LeftHatY) < -7500 && Xbox.getAnalogHat(0,RightHatY) < -7500) {
      targetOffset = scale(Xbox.getAnalogHat(0,LeftHatY)+Xbox.getAnalogHat(0,RightHatY),-7500,-32768,0,7); // Scale from -7500 to -32768 to 0-7
      steerForward = true;
    } else if(Xbox.getAnalogHat(0,LeftHatY) > 7500 && Xbox.getAnalogHat(0,RightHatY) > 7500) {
      targetOffset = scale(Xbox.getAnalogHat(0,LeftHatY)+Xbox.getAnalogHat(0,RightHatY),7500,32767,0,7); // Scale from 7500-32767 to 0-7
      steerBackward = true;
    }/*
    if(((long)Xbox.getAnalogHat(LeftHatY) - (long)Xbox.getAnalogHat(RightHatY)) > 15) {
      turningOffset = scale(abs(Xbox.getAnalogHat(LeftHatY) - Xbox.getAnalogHat(RightHatY)),0,255,0,20); // Scale from 0-255 to 0-20
       steerLeft = true;      
    } else if (((long)Xbox.getAnalogHat(RightHatY) - (long)Xbox.getAnalogHat(LeftHatY)) > 15) {   
      turningOffset = scale(abs(Xbox.getAnalogHat(LeftHatY) - Xbox.getAnalogHat(RightHatY)),0,255,0,20); // Scale from 0-255 to 0-20  
      steerRight = true;  
    }*/
  }
  
  else if(command == stop) {
    steerStop = true;    
    if(lastCommand != stop) { // Set new stop position
      targetPosition = wheelPosition;
      stopped = false;
    }
  }
  lastCommand = command;
}
double scale(double input, double inputMin, double inputMax, double outputMin, double outputMax) { // Like map() just returns a double
  double output;
  if(inputMin < inputMax)
    output = (input-inputMin)/((inputMax-inputMin)/(outputMax-outputMin));              
  else
    output = (inputMin-input)/((inputMin-inputMax)/(outputMax-outputMin));
  if(output > outputMax)
    output = outputMax;
  else if(output < outputMin)
    output = outputMin;
  return output;
}
void stopAndReset() {
  stopMotor(left);
  stopMotor(right);  
  lastError = 0;
  iTerm = 0;
  targetPosition = wheelPosition;
}
double getGyroYrate() {
  // (gyroAdc-gyroZero)/Sensitivity (In quids) - Sensitivity = 0.00333/3.3*1023=1.0323
  double gyroRate = -((double)((double)analogRead(gyroY) - zeroValues[0]) / 1.0323);
  return gyroRate;
}
double getAccY() {
  double accYval = ((double)analogRead(accY) - zeroValues[1]);  
  double accZval = ((double)analogRead(accZ) - zeroValues[2]);
  // Convert to 360 degrees resolution
  // atan2 outputs the value of -π to π (radians) - see http://en.wikipedia.org/wiki/Atan2
  // We are then convert it to 0 to 2π and then from radians to degrees
  return (atan2(-accYval,-accZval)+PI)*RAD_TO_DEG;
}
void calibrateSensors() {
  for (uint8_t i = 0; i < 100; i++) { // Take the average of 100 readings
    zeroValues[0] += analogRead(gyroY);
    zeroValues[1] += analogRead(accY);
    zeroValues[2] += analogRead(accZ);
    delay(10);
  }
  zeroValues[0] /= 100; // Gyro X-axis
  zeroValues[1] /= 100; // Accelerometer Y-axis
  zeroValues[2] /= 100; // Accelerometer Z-axis

  if(zeroValues[1] > 500) { // Check which side is lying down - 1g is equal to 0.33V or 102.3 quids (0.33/3.3*1023=102.3)
    zeroValues[1] -= 102.3; // +1g when lying at one of the sides
    kalman.setAngle(90); // It starts at 90 degress and 270 when facing the other way
    gyroAngle = 90;
  } else {
    zeroValues[1] += 102.3; // -1g when lying at the other side
    kalman.setAngle(270);
    gyroAngle = 270;
  }
}
void moveMotor(Command motor, Command direction, double speedRaw) { // Speed is a value in percentage 0-100%
  if(speedRaw > 100)
    speedRaw = 100;
  int speed = speedRaw*((double)PWMVALUE)/100; // Scale from 100 to PWMVALUE
  if (motor == left) {
    setPWM(leftPWM,speed); // Left motor pwm
    if (direction == forward) {
      cbi(leftPort,leftA);
      sbi(leftPort,leftB);
    } 
    else if (direction == backward) {
      sbi(leftPort,leftA);
      cbi(leftPort,leftB);
    }
  } 
  else if (motor == right) {
    setPWM(rightPWM,speed); // Right motor pwm
    if (direction == forward) {
      cbi(rightPort,rightA);
      sbi(rightPort,rightB);
    } 
    else if (direction == backward) {
      sbi(rightPort,rightA);
      cbi(rightPort,rightB);
    }
  }
}
void stopMotor(Command motor) {  
  if (motor == left) {
    setPWM(leftPWM,PWMVALUE); // Set high
    sbi(leftPort,leftA);
    sbi(leftPort,leftB);
  } 
  else if (motor == right) {
    setPWM(rightPWM,PWMVALUE); // Set high
    sbi(rightPort,rightA);
    sbi(rightPort,rightB);
  }
}
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

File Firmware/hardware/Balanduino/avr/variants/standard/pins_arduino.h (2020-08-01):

/*
  pins_arduino.h - Pin definition functions for Arduino
  Part of Arduino - http://www.arduino.cc/

  Copyright (c) 2007 David A. Mellis

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
  $Id: wiring.h 249 2007-02-03 16:52:51Z mellis $

  Changelog
  -----------
  11/25/11  - ryan@ryanmsutton.com - Add pins for Sanguino 644P and 1284P
  07/15/12  - ryan@ryanmsutton.com - Updated for arduino0101
  01/26/13  - kristianl@tkjelectronics.dk - Changed to work with Balanduino
*/

#ifndef Pins_Arduino_h
#define Pins_Arduino_h

#include <avr/pgmspace.h>

#define PIN_SPI_SS   (6)
#define PIN_SPI_MOSI (27)
#define PIN_SPI_MISO (28)
#define PIN_SPI_SCK  (29)

static const uint8_t SS   = PIN_SPI_SS;
static const uint8_t MOSI = PIN_SPI_MOSI;
static const uint8_t MISO = PIN_SPI_MISO;
static const uint8_t SCK  = PIN_SPI_SCK;

#define LED_BUILTIN 6

#define PIN_A0 (7)
#define PIN_A1 (8)
#define PIN_A2 (9)
#define PIN_A3 (10)
#define PIN_A4 (11)
#define PIN_A5 (12)

static const uint8_t A0 = PIN_A0;
static const uint8_t A1 = PIN_A1;
static const uint8_t A2 = PIN_A2;
static const uint8_t A3 = PIN_A3;
static const uint8_t A4 = PIN_A4;
static const uint8_t A5 = PIN_A5; // Not broken out - used for battery voltage measurement

#define PIN_WIRE_SDA (13)
#define PIN_WIRE_SCL (14)

static const uint8_t SDA = PIN_WIRE_SDA;
static const uint8_t SCL = PIN_WIRE_SCL;

// ATMEL ATMEGA1284P / Balanduino revision 1.2 or older
//
//                   +---\/---+
//   M2A (D25) PB0  1|        |40 PA0 (A0 / D7)
//   M2B (D26) PB1  2|        |39 PA1 (A1 / D8)
//   INT2 (D2) PB2  3|        |38 PA2 (A2 / D9)
// BUZZER (D5) PB3  4|        |37 PA3 (A3 / D10)
//    LED (D6) PB4  5|        |36 PA4 (A4 / D11)
//  MOSI (D27) PB5  6|        |35 PA5 (A5 / D12) VBAT
//  MISO (D28) PB6  7|        |34 PA6 (D30) EN1B
//   SCK (D29) PB7  8|        |33 PA7 (D31) EN2B
//             RST  9|        |32 AREF
//             VCC 10|        |31 GND
//             GND 11|        |30 AVCC
//           XTAL2 12|        |29 PC7 (D24) M1B
//           XTAL1 13|        |28 PC6 (D23) M1A
//     RX (D0) PD0 14|        |27 PC5 (D22) M2EN
//     TX (D1) PD1 15|        |26 PC4 (D21) M1EN
//  EN1A (D15) PD2 16|        |25 PC3 (D20) MAX_SS
//  EN2A (D16) PD3 17|        |24 PC2 (D19) MAX_INT
// PWM1B (D17) PD4 18|        |23 PC1 (D13) SDA
// PWM1A (D18) PD5 19|        |22 PC0 (D14) SCL
//  PWM2B (D3) PD6 20|        |21 PD7 (D4) PWM2A
//                   +--------+
//

// ATMEL ATMEGA1284P / Balanduino revision 1.3
//
//                   +---\/---+
//  EN1A (D25) PB0  1|        |40 PA0 (A0 / D7)
//  EN1B (D26) PB1  2|        |39 PA1 (A1 / D8)
//   M2A (D15) PB2  3|        |38 PA2 (A2 / D9)
//   M2B (D16) PB3  4|        |37 PA3 (A3 / D10)
//    LED (D6) PB4  5|        |36 PA4 (A4 / D11) BUZZER
//  MOSI (D27) PB5  6|        |35 PA5 (A5 / D12) VBAT
//  MISO (D28) PB6  7|        |34 PA6 (D30) EN2A
//   SCK (D29) PB7  8|        |33 PA7 (D31) EN2B
//             RST  9|        |32 AREF
//             VCC 10|        |31 GND
//             GND 11|        |30 AVCC
//           XTAL2 12|        |29 PC7 (D24) M1B
//           XTAL1 13|        |28 PC6 (D23) M1A
//     RX (D0) PD0 14|        |27 PC5 (D22) M2EN
//     TX (D1) PD1 15|        |26 PC4 (D21) M1EN
//    RX1 (D2) PD2 16|        |25 PC3 (D20) MAX_SS
//    TX1 (D3) PD3 17|        |24 PC2 (D19) MAX_INT
// PWM1B (D17) PD4 18|        |23 PC1 (D13) SDA
// PWM1A (D18) PD5 19|        |22 PC0 (D14) SCL
//  PWM2B (D4) PD6 20|        |21 PD7 (D5) PWM2A
//                   +--------+
//

#define NUM_DIGITAL_PINS            26
#define NUM_ANALOG_INPUTS           6

#define analogInputToDigitalPin(p)  ((p < 6) ? (p) + 7 : -1)
#define analogPinToChannel(p)       ((p < 6) ? (p) : (p) - 7)

#if BALANDUINO_REVISION < 13
    #define digitalPinHasPWM(p)         ((((p) >= 3) && ((p) <= 6)) || (((p) >= 17) && ((p) <= 18)))
#else
    #define digitalPinHasPWM(p)         ((((p) >= 4) && ((p) <= 6)) || (((p) >= 16) && ((p) <= 18)))
#endif

#define digitalPinToPCICR(p)        ( (((p) >= 0) && ((p) <= 31)) ? (&PCICR) : ((uint8_t *)0) )
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

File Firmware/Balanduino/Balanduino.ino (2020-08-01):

/* Copyright (C) 2013-2015 Kristian Lauszus, TKJ Electronics. All rights reserved.

 This software may be distributed and modified under the terms of the GNU
 General Public License version 2 (GPL2) as published by the Free Software
 Foundation and appearing in the file GPL2.TXT included in the packaging of
 this file. Please note that GPL2 Section 2[b] requires that all works based
 on this software must also be made publicly available under the terms of
 the GPL2 ("Copyleft").

 Contact information
 -------------------

 Kristian Lauszus, TKJ Electronics
 Web      :  http://www.tkjelectronics.dk
 e-mail   :  kristianl@tkjelectronics.dk

 This is the algorithm for the Balanduino balancing robot.
 It can be controlled by either an Android app or a computer application via Bluetooth.
 The Android app can be found at the following link: https://github.com/TKJElectronics/BalanduinoAndroidApp
 The Processing application can be found here: https://github.com/TKJElectronics/BalanduinoProcessingApp
 A dedicated Windows application can be found here: https://github.com/TKJElectronics/BalanduinoWindowsApp
 It can also be controlled by a PS3, PS4, Wii or a Xbox controller.
 Furthermore it supports the Spektrum serial protocol used for RC receivers.
 For details, see: http://balanduino.net/
*/

/* Use this to enable and disable the different options */
#define ENABLE_TOOLS
#define ENABLE_SPP
#define ENABLE_PS3
#define ENABLE_PS4
#define ENABLE_WII
#define ENABLE_XBOX
#define ENABLE_ADK
#define ENABLE_SPEKTRUM

#include "Balanduino.h"
#include <Arduino.h> // Standard Arduino header
#include <Wire.h> // Official Arduino Wire library
#include <SPI.h> // Official Arduino SPI library

#ifdef ENABLE_ADK
#include <adk.h>
#endif

// These are all open source libraries written by Kristian Lauszus, TKJ Electronics
// The USB libraries are located at the following link: https://github.com/felis/USB_Host_Shield_2.0
#include <Kalman.h> // Kalman filter library - see: http://blog.tkjelectronics.dk/2012/09/a-practical-approach-to-kalman-filter-and-how-to-implement-it/

#ifdef ENABLE_XBOX
#include <XBOXRECV.h>
#endif
#ifdef ENABLE_SPP
#include <SPP.h>
#endif
#ifdef ENABLE_PS3
#include <PS3BT.h>
#endif
#ifdef ENABLE_PS4
#include <PS4BT.h>
#endif
#ifdef ENABLE_WII
#include <Wii.h>
#endif

// Create the Kalman library instance
Kalman kalman; // See https://github.com/TKJElectronics/KalmanFilter for source code

#if defined(ENABLE_SPP) || defined(ENABLE_PS3) || defined(ENABLE_PS4) || defined(ENABLE_WII) || defined(ENABLE_XBOX) || defined(ENABLE_ADK)
#define ENABLE_USB
USB Usb; // This will take care of all USB communication
#else
#define _usb_h_ // Workaround include trap in the USB Host library
#include <avrpins.h> // Include this from the USB Host library
#endif

#ifdef ENABLE_ADK
// Implementation for the Android Open Accessory Protocol. Simply connect your phone to get redirected to the Play Store
ADK adk(&Usb, "TKJ Electronics", // Manufacturer Name
              "Balanduino", // Model Name
              "Android App for Balanduino", // Description - user visible string
              "0.6.3", // Version of the Android app
              "https://play.google.com/store/apps/details?id=com.tkjelectronics.balanduino", // URL - web page to visit if no installed apps support the accessory
              "1234"); // Serial Number - this is not used
#endif

#ifdef ENABLE_XBOX
XBOXRECV Xbox(&Usb); // You have to connect a Xbox wireless receiver to the Arduino to control it with a wireless Xbox controller
#endif

#if defined(ENABLE_SPP) || defined(ENABLE_PS3) || defined(ENABLE_PS4) || defined(ENABLE_WII)
#define ENABLE_BTD
#include <usbhub.h> // Some dongles can have a hub inside
USBHub Hub(&Usb); // Some dongles have a hub inside
BTD Btd(&Usb); // This is the main Bluetooth library, it will take care of all the USB and HCI communication with the Bluetooth dongle
#endif

#ifdef ENABLE_SPP
SPP SerialBT(&Btd, "Balanduino", "0000"); // The SPP (Serial Port Protocol) emulates a virtual Serial port, which is supported by most computers and mobile phones
#endif

#ifdef ENABLE_PS3
PS3BT PS3(&Btd); // The PS3 library supports all three official controllers: the Dualshock 3, Navigation and Move controller
#endif

#ifdef ENABLE_PS4
//PS4BT PS4(&Btd, PAIR); // You should create the instance like this if you want to pair with a PS4 controller, then hold PS and Share on the PS4 controller
// Or you can simply send "CPP;" to the robot to start the pairing sequence
// This can also be done using the Android or via the serial port
PS4BT PS4(&Btd); // The PS4BT library supports the PS4 controller via Bluetooth
#endif

#ifdef ENABLE_WII
WII Wii(&Btd); // The Wii library can communicate with Wiimotes and the Nunchuck and Motion Plus extension and finally the Wii U Pro Controller
//WII Wii(&Btd,PAIR); // You will have to pair with your Wiimote first by creating the instance like this and the press 1+2 on the Wiimote or press sync if you are using a Wii U Pro Controller
// Or you can simply send "CPW;" to the robot to start the pairing sequence
// This can also be done using the Android or via the serial port
#endif
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

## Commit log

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2013-02-02 You can now disconnect the controller when the SPP connection is established and several other fixes
    [Balanduino.h, Balanduino.ino]
2013-02-04 Replaced a lot of defines with const. See: http://arduino.cc/en/Reference/Const
    [Balanduino.h, Balanduino.ino]
2013-02-04 Wii U Pro Controller joysticks where swapped around
    [Balanduino.ino]
2013-02-09 Interrupt on CHANGE for the double amount of resolution
2013-02-10 Limit restAngle if it's too big compared to last loop
    [Balanduino.h, Balanduino.ino, Bluetooth.ino]
2013-02-13 Fixed comments and a lot of whitespace
    [Balanduino.h, Balanduino.ino, Bluetooth.ino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]
2013-02-14 Run the loop as fast as possible and not in a timed fixed loop
    [Balanduino.h, Balanduino.ino, Bluetooth.ino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]
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2013-02-16 Fixed support for Xbox controller
    [Bluetooth.ino]
2013-02-16 Left and right were swapped
    [Bluetooth.ino]
2013-02-17 Read from Wiimote much more often to prevent lag
    [Balanduino.h, Balanduino.ino]
2013-02-19 Set fuse bit correctly
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2013-02-24 Overbalance fixed due to positionError vs wheelVelocity
    [Balanduino.h, Balanduino.ino, Bluetooth.ino]
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2013-03-25 Reset gyro angle automatically
    [Balanduino.ino]
2013-03-31 Show battery status of controllers using the LEDs
2013-04-16 Added frame drawings
    [Bottom layer.DXF, Bottom layer.SLDPRT, Middle layer.DXF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]
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2013-04-16 Added a copy of boards.txt inside avr folder
2013-04-18 Added link to Arduino page about sketchbook folder
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2013-04-28 Fix the 0-360 transition problem when the accelerometer angle jumps between 0 and 360 degrees
    [Balanduino.h, Balanduino.ino]
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2013-04-30 Will now measure battery voltage via a voltage divider
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2013-05-03 New versions of Arduino will report ram usage: https://github.com/arduino/Arduino/pull/1377
2013-05-06 The SPP Class now inherit from the Arduino Stream library
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2013-05-07 Read SPP data in a separate function in case it returns
2013-05-13 Can now control the robot using the accelerometer inside the PS3 controller too
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2013-06-10 Fixed latency issue with Wiimote
    [Balanduino.h, Balanduino.ino]
2013-06-15 Print error if I2C fails
    [I2C.ino]
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2013-07-14 Check is Bluetooth dongle is connected before blinking LED
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2013-07-16 Show if PS3 is charging using the LEDs on the controller
2013-07-18 Make sure the LED is turned off it the dongle is unplugged
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2013-07-19 EEPROM version should be able to vary in length without problems
    [EEPROM.ino]
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2013-07-19 Updated PID library function to start with a capital letter to match the style of the existing functions
2013-07-19 New version of USB Host library will update battery level automatically when getBatteryLevel is called
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2013-08-02 Reference the standard Arduino core when using Arduino 1.5.x
    This is possible after https://github.com/arduino/Arduino/pull/1368 got merged
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2013-08-04 Don't reset timer when setting information
    [Bluetooth.ino]
2013-08-12 SCL and SDA pin has changed pins on new PCB
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2013-08-31 Added a comment about I2C errors
    [I2C.ino]
2013-09-01 Changed buzzer to oscillator-type. Enabled battery-voltage measurement for PCB V1.1.
    [Balanduino.ino, pins_arduino.h]
2013-09-01 Added new frame and PCB
    [Bottom layer.DXF, Bottom layer.SLDPRT, Bottom_layer-V1.DXF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]
2013-09-03 Use Wire library bundled with the Arduino IDE
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2013-09-04 The new Balanduino main board can handle a baud rate of 115200
2013-09-04 Part of https://github.com/arduino/Arduino/issues/1176 is now fixed
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2013-09-04 Because of the ATmega1284P the entire code can now be enabled without problems
    [Balanduino.ino]
2013-09-04 There is no need to check battery level that often
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2013-09-05 The user is now able to set the different values via UART as well
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2013-09-12 Send out EEPROM version and send battery level and runtime every 500ms
2013-09-13 Updated core to the one in Arduino 1.5.4
2013-09-14 Retry initialization if the USB device returns an error
    This is needed for some dongles
    [Balanduino.ino, Bluetooth.ino]
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2013-10-05 Defined ARDUINO_AVR_BALANDUINO in makefile
    This is used in the USB Host library
2013-10-05 Defined encoder port and mask in header file instead of hardcoding it in Motor.ino
2013-10-08 There is no need to reset state machine all the way back
    [Bluetooth.ino]
2013-10-22 Added PID and VID in boards.txt
    Will be used in future versions of the Arduino IDE to auto detect the Balanduino
2013-10-23 Reduced number of calls to mills() and micros()
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2013-11-11 Can now disconnect Xbox wireless controller
    Also updated the way the LEDs and rumble is turned on the Xbox controller
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2013-11-12 Added SERIAL metadata into variant files - see: https://github.com/arduino/Arduino/commit/e7c24c66a931c9a06e89cd2f61baffc00af0d238
2013-11-15 Removed board entry for ATmega644, as it was only used for the prototype
2013-11-16 The location of the Wire library was move again - see: https://github.com/arduino/Arduino/commit/9a9652d5063c9279f34aa7055651ee139976e737
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2013-12-15 Increased I2C frequency to 400kHz
    Decreases loop time from approx. 3.3 to 2.5 ms
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2013-12-16 Toggle VBUS if USB fails
    [Bluetooth.ino]
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2013-12-21 Indicate if EEPROM values are reset using the buzzer
    [Balanduino.ino]
2013-12-21 Scale values properly
    Fix for: 9a45a1f32b49f9c34bee6437831e1116a196f1ad
    [Bluetooth.ino]
2013-12-22 Interrupt on encoder pin change interrupt as well
    This doubles the encoder resolution
2013-12-22 Added missing function prototypes
    [Balanduino.h]
2013-12-22 Allow pins to be on different pin change interrupt vectors
2013-12-22 Fixed digitalPinToPCMSKbit macro for pin 13 and 14
    They were swapped around
    [pins_arduino.h]
2013-12-22 Don’t store encoder lookup table in flash, as this is slower
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2013-12-26 Use Timer3 on the Balanduino, as Timer1 is used for PWM for the motors
2013-12-30 Fixed link to ATmega1284P datasheet
    [Balanduino.ino]
2013-12-30 Added information about modified Servo library and why it is needed
2013-12-31 It is now possible to turn the LED off, by using the new enum
    Before you had to call setLedOff
2014-01-01 Use MAKE_PIN macro to write directly to the port registers when using the LED as well
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2014-01-22 Can now control the robot using the accelerometer inside the PS4 controller
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2014-02-20 Revert "Pins definitions are now #defines"
    This reverts commit c926f829c47d5c5f6dcb33e1b0a4422fdadadaf0.
    [pins_arduino.h]
2014-02-20 Forgot to add Timer3 to variant file after upgrade to ATmega1284P
2014-02-25 Keep trying to calibrate gyro until it is standing still
2014-02-26 Fixed some text in the schematic
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2014-02-28 Forgot to add a check if tools were enabled before printing the menu
2014-03-02 Include the standard Arduino header in the sketch
    This is needed if none of the libraries is used and you are using the make file
2014-03-02 Rearrange somecode
    Moved buzzer define up to the rest and moved printMenu() down to the bottom of setup()
    [Balanduino.h, Balanduino.ino]
2014-03-02 Reset MPU-6050 in setup
    Inspired by: https://github.com/Lauszus/multiwii-firmware/blob/master/Sensors.cpp
    [Balanduino.ino]
2014-03-02 Enabled Digital Low Pass Filter (DLPF) on the MPU-6050
    Still needs some testing
2014-03-02 https://github.com/arduino/Arduino/issues/1176 is now fixed
2014-03-03 Spektrum code can now bind with satellite receiver, detect if it starts in the middle of a frame and be used together with TOOLS
2014-03-07 Beep long when EEPROM values are reset instead of two short beeps
    [Balanduino.ino]
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2014-03-21 Uploaded a pdf version of the V1.2 schematic
2014-03-27 A little more verbose error message
    Some people don't realize that it's just fine to use the "beta" version
    [Balanduino.h]
2014-04-23 Turn on rumble when the PS4 controller is connected, then indicate battery level using the LED light
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2014-08-21 Swapped encoder1 and encoder2 pins in encoder reading, as leftEncoder1 was located on bit0 in the new revision of the PCB
    This needs testing
    [Motor.ino]
2014-08-21 Encoders has to be inverted after: 8b078c4823cff87c15c3fd38b091437d779ca07e
    This was expected
    [Motor.ino]
2014-08-22 Inline interrupt functions on new revision of PCB
    This improves speed and reduces code size!
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2015-04-19 Update to newest version of Kalman filter and USB Host Shield library
    USB Host Shield library now uses the official SPI library and it has to be included in the sketch as well due to a bug in the Arduino IDE
    [Balanduino.ino]
2015-04-19 Replace all doubles with float
    Does not have any effect on AVR microcontroller, but might have on any bores using a ARM processor
    [Balanduino.h, Balanduino.ino, Bluetooth.ino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]
2015-04-19 Fixed bug where accAngle were reinitialised
    For some reason it has been working anyway
    [Balanduino.ino]
2015-04-29 Fixed: warning: 'static' is not at beginning of declaration
    [pins_arduino.h]
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2015-05-04 Moved libraries submodules inside hardware add-on
    This allows them to be automatically included when using the Arduino Boards manager
2015-05-04 Added package_balanduino_index.json to project
    This is used by the Arduino Boards Manager
2015-06-16 Added Frame V3 which is the most recent used for manufacturing.
    [Bottom layer_V3.DXF, Bottom layer_V3.SLDPRT, Middle layer_V3.DXF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]
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2016-08-17 Add tools field to package_tkj_balanduino_index.json
    The missing tools field causes Arduino IDE 1.6.11 to not start if the Balanduino boards package was installed in a previous version of the Arduino IDE. If you attempt to install the Balanduino boards package using Boards Manager in Arduino IDE 1.6.11 it fails with a java.lang.NullPointerException error.
2016-10-26 Add PIN defines, so the pins can easily be used by external libraries
    See: https://github.com/arduino/Arduino/pull/4814
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

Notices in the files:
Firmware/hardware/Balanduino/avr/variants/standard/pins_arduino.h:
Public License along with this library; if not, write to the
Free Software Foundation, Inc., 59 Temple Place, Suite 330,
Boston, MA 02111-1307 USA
